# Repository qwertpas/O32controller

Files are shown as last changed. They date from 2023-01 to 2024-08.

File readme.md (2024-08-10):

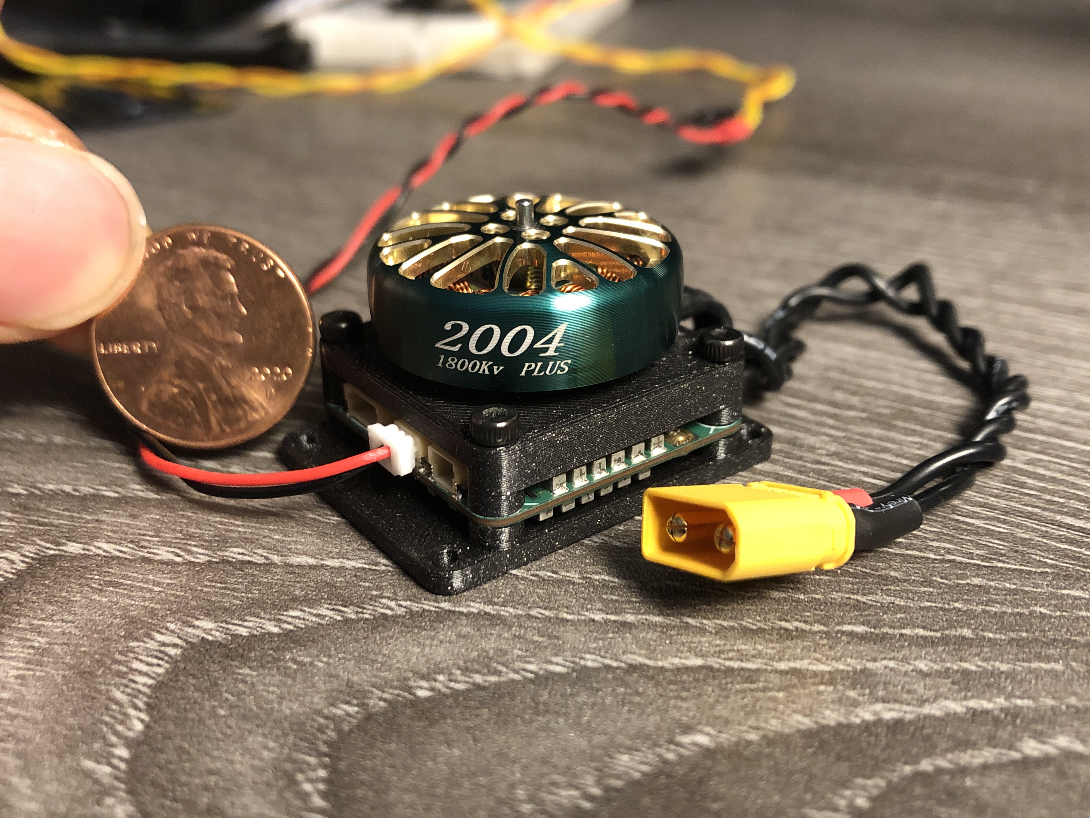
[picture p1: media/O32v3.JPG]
BR2304

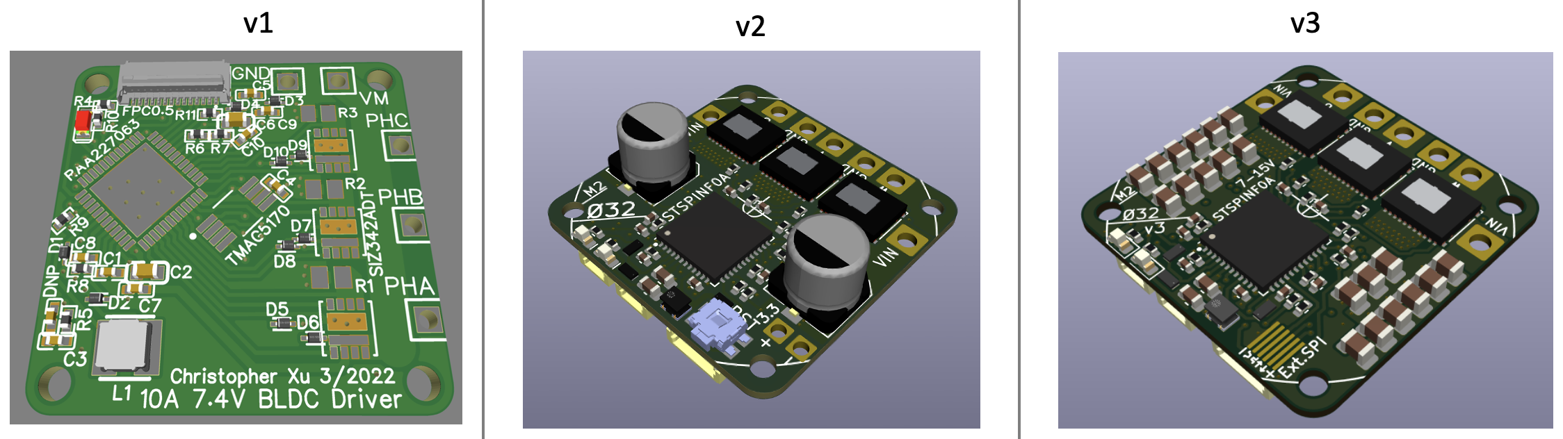
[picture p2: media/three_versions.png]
threeversions


Small robots often use servos or small brushed DC motors, but they are not as power dense as the brushless DC (BLDC) motors commonly found in drones. Called the Ø32 because the M2 mounting holes are on a 32mm diameter circle, this project controls 7-15V motors with accurate position feedback and field-oriented control (FOC), while fitting almost completely behind a 2304 or larger drone motor.

Specs:
- 27mm x 27mm x 0.8mm, 4-layer, 1oz copper PCB
- M2 mounting holes on a 32mm diameter circle
- 7-15V input, bus voltage sensing
- MCU internal temperature sensor and external NTC reading
- built-in high speed 12-bit magnetic angle sensor and external SPI encoder port (3.3V)
- 3 shunt current sensing and overcurrent protection 
- 2x 2-pin JST-SH connectors for RS-485 communication, allowing daisy chaining
- 1x 4-pin JST-SH connector for SWD programming/debug and UART_TX output
- FOC capable

Critical components:
- STSPIN32F0A BLDC gate driver and Cortex-M0 MCU
- MA702 magnetic angle sensor
- CSD88584Q5DC half-bridge (50A continuous)

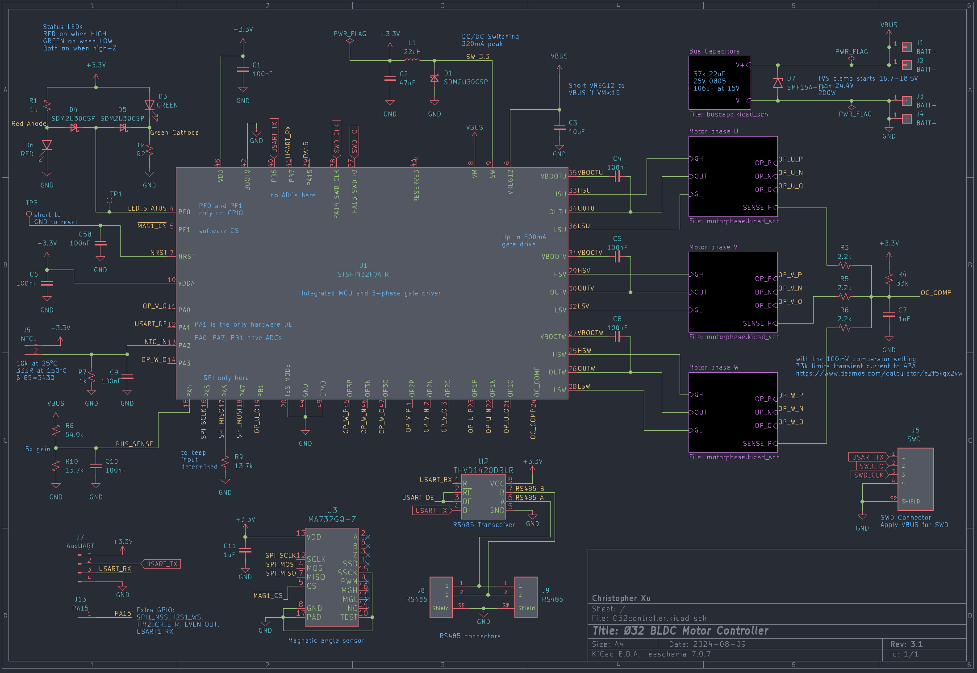
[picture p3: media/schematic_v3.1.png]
schematic

[Full schematic PDF](https://github.com/qwertpas/O32controller/blob/master/v3/output_v3.1/O32controller.pdf)

More info on Hackaday.io: https://hackaday.io/project/189115-32-bldc-controller

Firmware here: https://github.com/qwertpas/O32controller_FW

Changelog from v3 to v3.1:
- Larger 15V TVS diode D2 (SMF15A) because there is space 
- Changed R4 from 121kΩ to 33kΩ for a more reasonable phase current limit of 43A using the 100mV comparator 
- Replaced external SPI pads with UART and GPIO PA15 pads for direct communication with another microcontroller without need for RS485 transceiver 
- Replace MA702 (12-bit magnetic encoder) with MA732 (14-bit, adjustable filter)
- Picked out parts in stock from LCSC as much as possible

Changelog from v2 to v3:
- Fixed TVS diode direction on VBUS (!!)
- Changed to 37x 22uF ceramic capacitors instead of 2x 100uF electrolytic capacitors for a thinner PCBA
- Removed I2C (formerly on PB6 and PB7)
- Moved UART_TX and UART_RX to PB6 and PB7 (formerly on PA2 and PA15)
- Changed PA2 to ADC1 CH2 to read a 10k NTC, soldered to pads
- Changed PA15 to GPIO for external SPI CS (MAG2_CS)
- Added 13.7k pulldown on SPI_MISO to keep it determined when no devices selected
- Changed to 100nF filter capacitor on BUS_SENSE instead of 1nF to charge ADC capacitor better and for smoother data
- Changed BUS_SENSE gain to 5x instead of 5.12x to reuse 13.7k resistor
- Removed test point on BUS_SENSE
- Added test point on LED_STATUS (for debugging using GPIO)
- Removed NRST pushbutton to create space
- Added 6 pads with 0.5mm pitch to solder FFC cable for an external SPI encoder
- Changed vias to 0.25mm hole size and 0.55mm plated diameter instead of 0.2/0.5 for easier manufacturability
- Changed minimum track clearance from 0.2mm to 0.16mm to make space for larger vias
- Changed to equal number of vias (27) on the top side of all three shunt resistors
- Changed most silkscreen text to 0.8mm width/height
- Put all footprints and 3D models in project library O32controller

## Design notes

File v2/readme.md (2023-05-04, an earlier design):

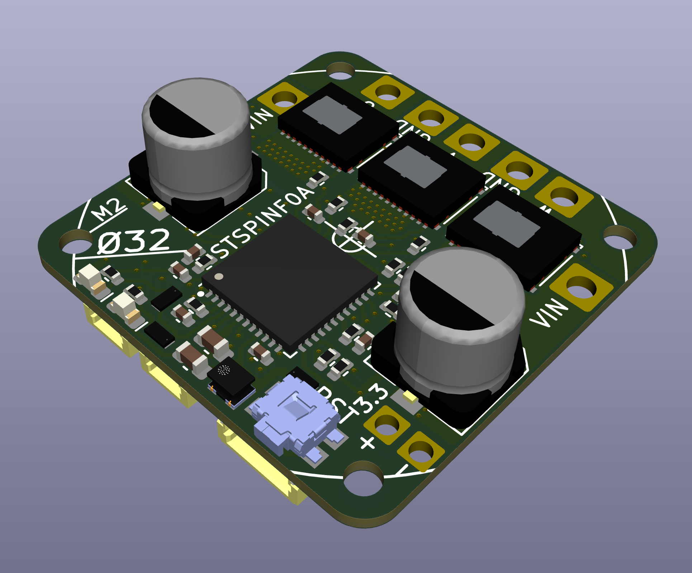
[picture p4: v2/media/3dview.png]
3dview


a brushless DC motor controller that fits behind a small drone motor (mounting holes are 32mm in diameter)

Board components are rated for 15V, 50A continuous and 110A for 10 seconds.  

Firmware here: https://github.com/qwertpas/O32controller_FW

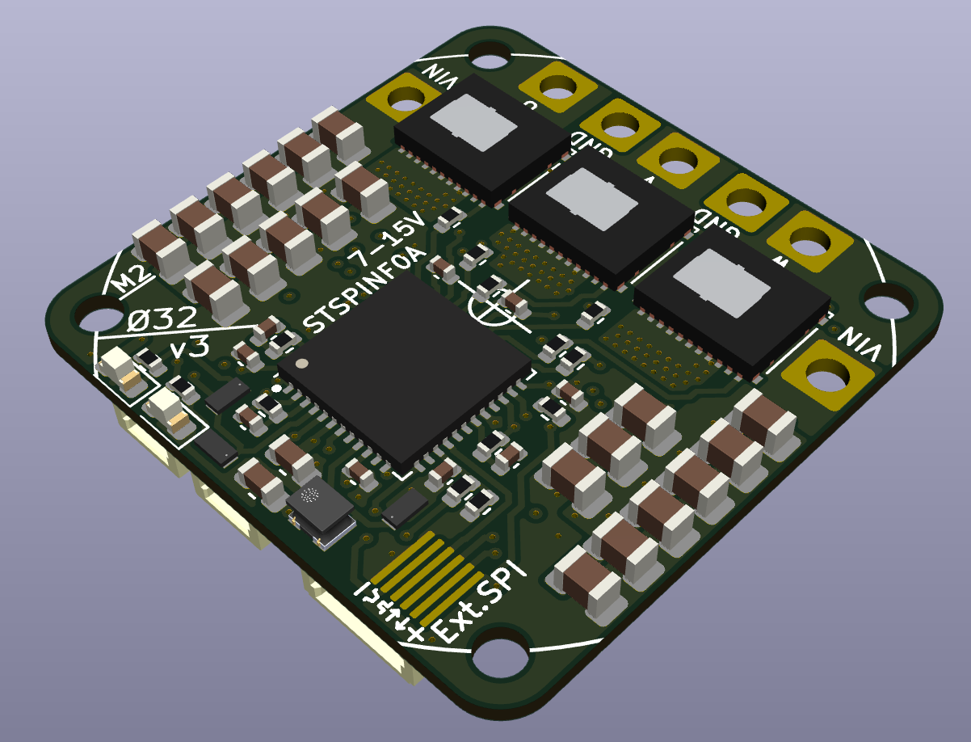
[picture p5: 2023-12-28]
media/v3_3d_front.png

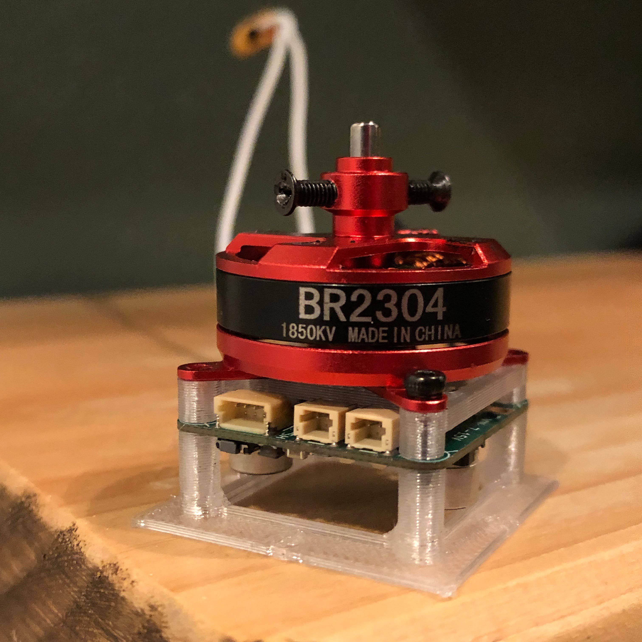
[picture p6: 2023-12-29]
media/O32_BR2304.jpeg

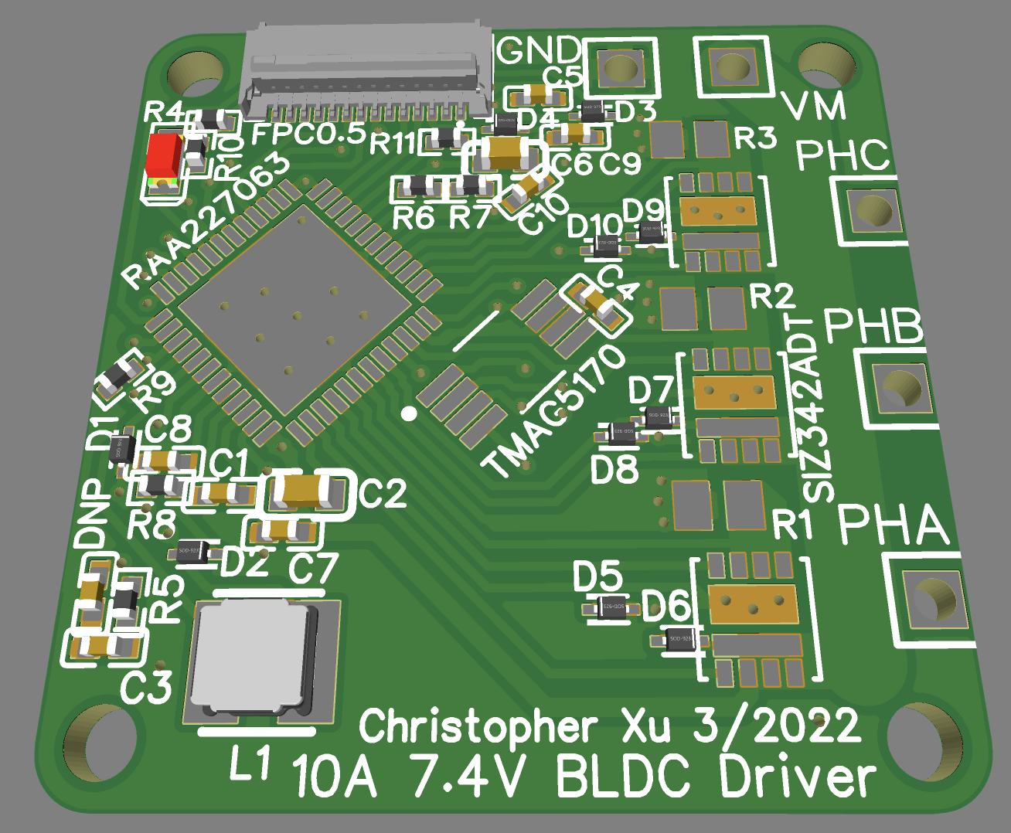
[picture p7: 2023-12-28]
media/v1_3d_front.png

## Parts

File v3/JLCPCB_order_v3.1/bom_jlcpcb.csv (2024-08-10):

Comment | Designator | Footprint | LCSC
100nF | C1,C4,C5,C6,C8,C9,C10,C58 | Capacitor_SMD:C_0402_1005Metric | C307331
1uF | C11 | Capacitor_SMD:C_0402_1005Metric | C52923
10nF | C12,C15,C18 | Capacitor_SMD:C_0402_1005Metric | C15195
4.7nF | C13,C16,C19 | Capacitor_SMD:C_0402_1005Metric | C1538
47uF | C2 | Capacitor_SMD:C_0603_1608Metric | C140782
22uF | C21,C22,C23,C24,C25,C26,C27,C28,C29,C30,C31,C32,C33,C34,C35,C36,C37,C38,C39,C40,C41,C42,C43,C44,C45,C46,C47,C48,C49,C50,C51,C52,C53,C54,C55,C56,C57 | O32controller:C_0805_nosilk | C45783
10uF | C3 | Capacitor_SMD:C_0603_1608Metric | C194427
1nF | C7,C14,C17,C20 | Capacitor_SMD:C_0402_1005Metric | C1523
SDM2U30CSP | D1,D4,D5 | O32controller:SDM2U30CSP-7
GREEN | D3 | LED_SMD:LED_0603_1608Metric | C125098
RED | D6 | LED_SMD:LED_0603_1608Metric | C2286
SMF15A-TP | D7 | Diode_SMD:D_SMF | C914420
SWD | J6 | O32controller:JST_SM04B-SRSS-TB(LF)(SN)
RS485 | J8,J9 | O32controller:JST_SM02B-SRSS-TB(LF)(SN) | C160402
22uH | L1 | O32controller:IND_VLS201612CX-220M-1 | C2044426
CSD88584Q5DC | Q1,Q2,Q3 | O32controller:CSD88584Q5DCT
1k | R1,R2,R7 | Resistor_SMD:R_0402_1005Metric | C11702
10R | R11,R13,R20,R22,R29,R31 | Resistor_SMD:R_0402_1005Metric | C854481
2.2R | R12,R21,R30 | Resistor_SMD:R_0402_1005Metric | C131536
27.4k | R14,R16,R23,R25,R32,R34 | Resistor_SMD:R_0402_1005Metric | C273730
1.78k | R15,R17,R24,R26,R33,R35 | Resistor_SMD:R_0402_1005Metric | C284379
PU2512FKMP50R002L | R18,R27,R36 | O32controller:R_Shunt_2512_6332Metric | C2090861
2.2k | R3,R5,R6 | Resistor_SMD:R_0402_1005Metric | C25879
33k | R4 | Resistor_SMD:R_0402_1005Metric | C25779
54.9k | R8 | Resistor_SMD:R_0402_1005Metric | C137959
13.7k | R9,R10,R19,R28,R37 | Resistor_SMD:R_0402_1005Metric | C274888
STSPIN32F0ATR | U1 | O32controller:VFQFPN-48-1EP_7x7mm_P0.5mm_EP2.8x2.8mm | C2651733
THVD1420DRLR | U2 | O32controller:THVD1420DRLR_SOT-585
MA732GQ-Z | U3 | O32controller:QFN-16_MA732

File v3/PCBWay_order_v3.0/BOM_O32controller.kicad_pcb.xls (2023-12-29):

designator | quantity | value | pack | mpn | mount_type
C1, C10, C4, C5, C58, C6, C8, C9 | 8 | 100nF | C_0402_1005Metric | CL05A104KA5NNNC | smt
C11 | 1 | 1uF | C_0402_1005Metric | GCM155C71A105KE38D | smt
C12, C15, C18 | 3 | 10nF | C_0402_1005Metric | CL05B103KB5NNNC | smt
C13, C16, C19 | 3 | 4.7nF | C_0402_1005Metric | GRM155R72A472KA01D | smt
C14, C17, C20, C7 | 4 | 1nF | C_0402_1005Metric | CC0402MRX7R9BB102 | smt
C2 | 1 | 47uF | C_0603_1608Metric | GRM188R60J476ME15D | smt
C21, C22, C23, C24, C25, C26, C27, C28, C29, C30, C31, C32, C33, C34, C35, C36, C37, C38, C39, C40, C41, C42, C43, C44, C45, C46, C47, C48, C49, C50, C51, C52, C53, C54, C55, C56, C57 | 37 | 22uF | C_0805_nosilk | CL21A226MAQNNNE | smt
C3 | 1 | 10uF | C_0603_1608Metric | GRM188R6YA106MA73D | smt
D1, D4, D5 | 3 | SDM2U30CSP | SDM2U30CSP-7 | SDM2U30CSP-7 | smt
D2 | 1 | ESDA17P20-1F2 | SMT2_0P91X0P63_STM-L | ESDA17P20-1F2 | smt
D3 | 1 | GREEN | LED_0603_1608Metric | LTST-C191KGKT | smt
D6 | 1 | RED | LED_0603_1608Metric | LTST-C191KRKT | smt
J1, J2 | 2 | BATT+ | SolderWire-Actual_1x01_D1.7mm_OD_2.75mm |  | tht
J10, J11, J12 | 3 | Motor Connection | SolderWire-Actual_1x01_D1.7mm_OD_2.75mm |  | tht
J3, J4 | 2 | BATT- | SolderWire-Actual_1x01_D1.7mm_OD_2.75mm |  | tht
J5 | 1 | NTC | SolderNTC-1.27mm |  | tht
J6 | 1 | SWD | JST_SM04B-SRSS-TB(LF)(SN) | SM04B-SRSS-TB(LF)(SN) | smt
J7 | 1 | ExternalSPI | FFC_0.5mm_6p |  | tht
J8, J9 | 2 | RS485 | JST_SM02B-SRSS-TB(LF)(SN) | SM02B-SRSS-TB_LF__SN_ | smt
L1 | 1 | 22uH | IND_VLS201612CX-220M-1 | VLS201612CX-220M-1 | smt
NT1, NT2, NT3 | 3 | Sense_N | NetTie-2_SMD_Pad0.25mm |  | tht
Q1, Q2, Q3 | 3 | CSD88584Q5DC | CSD88584Q5DCT | CSD88584Q5DC | smt
R1, R2, R7 | 3 | 1k | R_0402_1005Metric | RC0402FR-071KL | smt
R10, R19, R28, R37, R9 | 5 | 13.7k | R_0402_1005Metric | RC0402FR-0713K7L | smt
R11, R13, R20, R22, R29, R31 | 6 | 10R | R_0402_1005Metric | SR0402FR-7T10RL | smt
R12, R21, R30 | 3 | 2.2R | R_0402_1005Metric | CRCW04022R20JNEDHP | smt
R14, R16, R23, R25, R32, R34 | 6 | 27.4k | R_0402_1005Metric | RC0402FR-0727K4L | smt
R15, R17, R24, R26, R33, R35 | 6 | 1.78k | R_0402_1005Metric | RC0402FR-071K78L | smt
R18, R27, R36 | 3 | PU2512FKMP50R002L | R_Shunt_2512_6332Metric | PU2512FKMP50R002L | smt
R3, R5, R6 | 3 | 2.2k | R_0402_1005Metric | RC0402FR-072K2L | smt
R4 | 1 | 121k | R_0402_1005Metric | AF0402FR-07121KL | smt
R8 | 1 | 54.9k | R_0402_1005Metric | RC0402FR-0754K9L | smt
TP1, TP3 | 2 | TestPoint | TestPoint_Pad_Rect |  | tht
U1 | 1 | STSPIN32F0ATR | VFQFPN-48-1EP_7x7mm_P0.5mm_EP2.8x2.8mm | STSPIN32F0ATR | smt
U2 | 1 | THVD1420DRLR | THVD1420DRLR_SOT-585 | THVD1420DRLR | smt
U3 | 1 | MA702GQ-P | MA702GQ-P | MA702GQ-P | smt

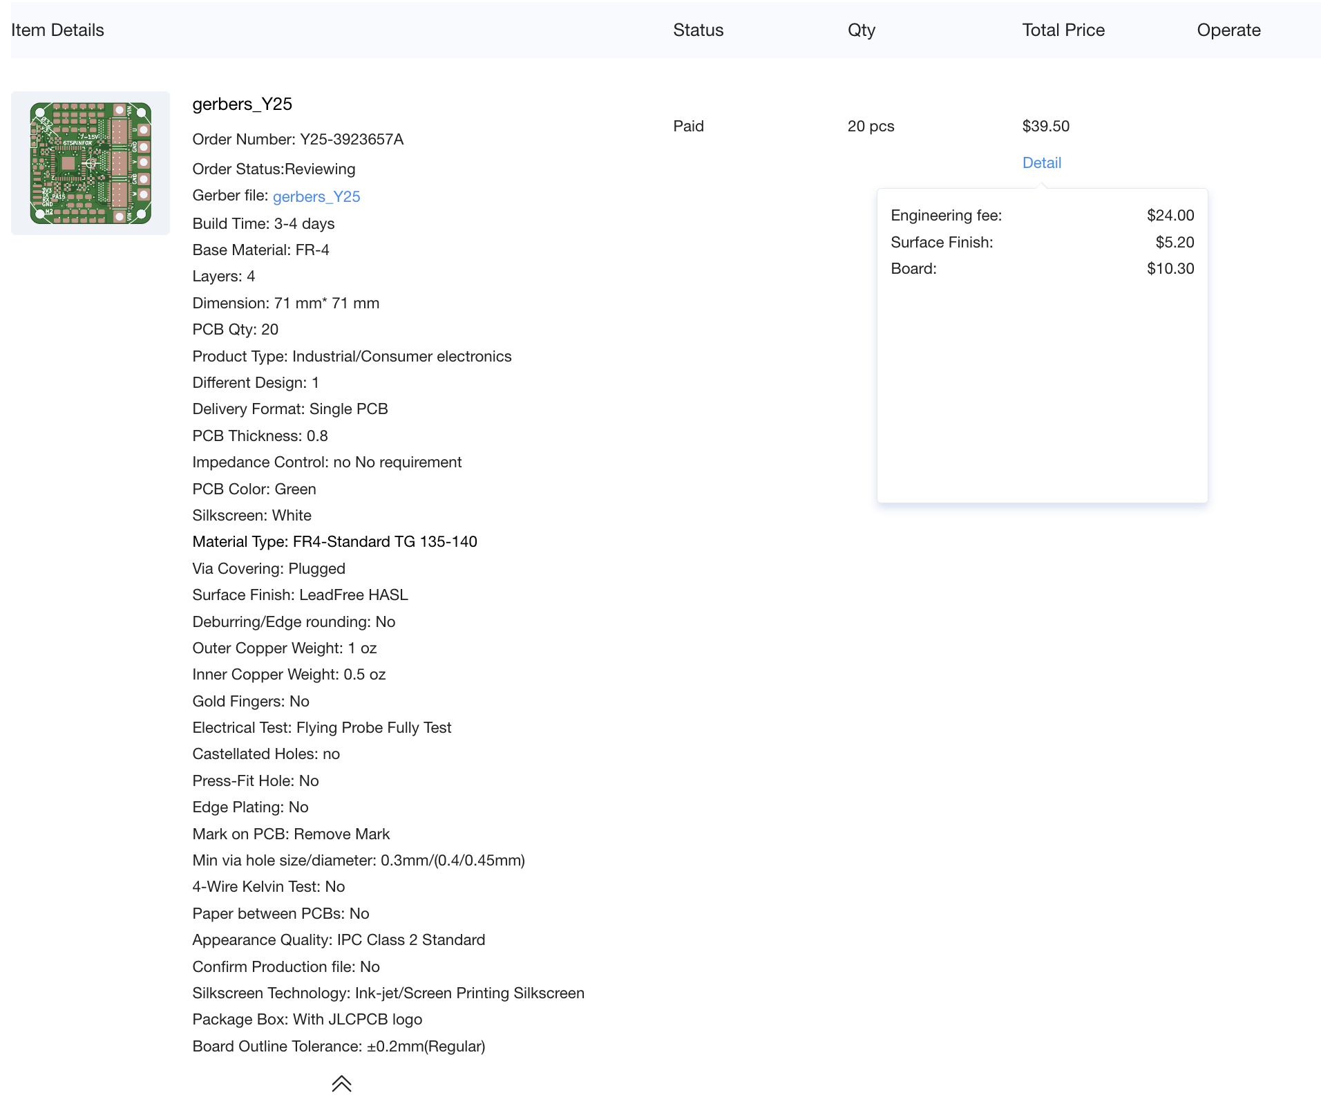
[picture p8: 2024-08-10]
v3/JLCPCB_order_v3.1/pcb_order.png

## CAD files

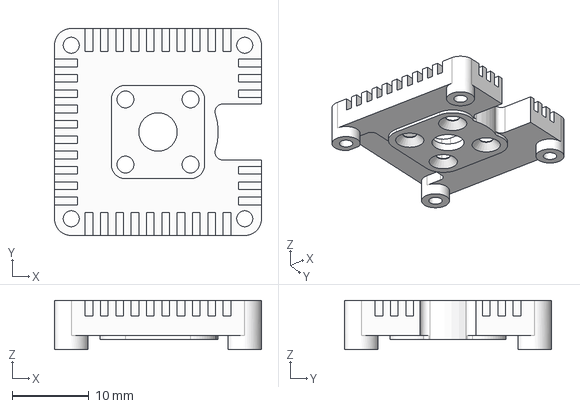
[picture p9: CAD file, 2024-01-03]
heatsinks/greenmount.step
27.0 x 27.0 x 6.40 mm

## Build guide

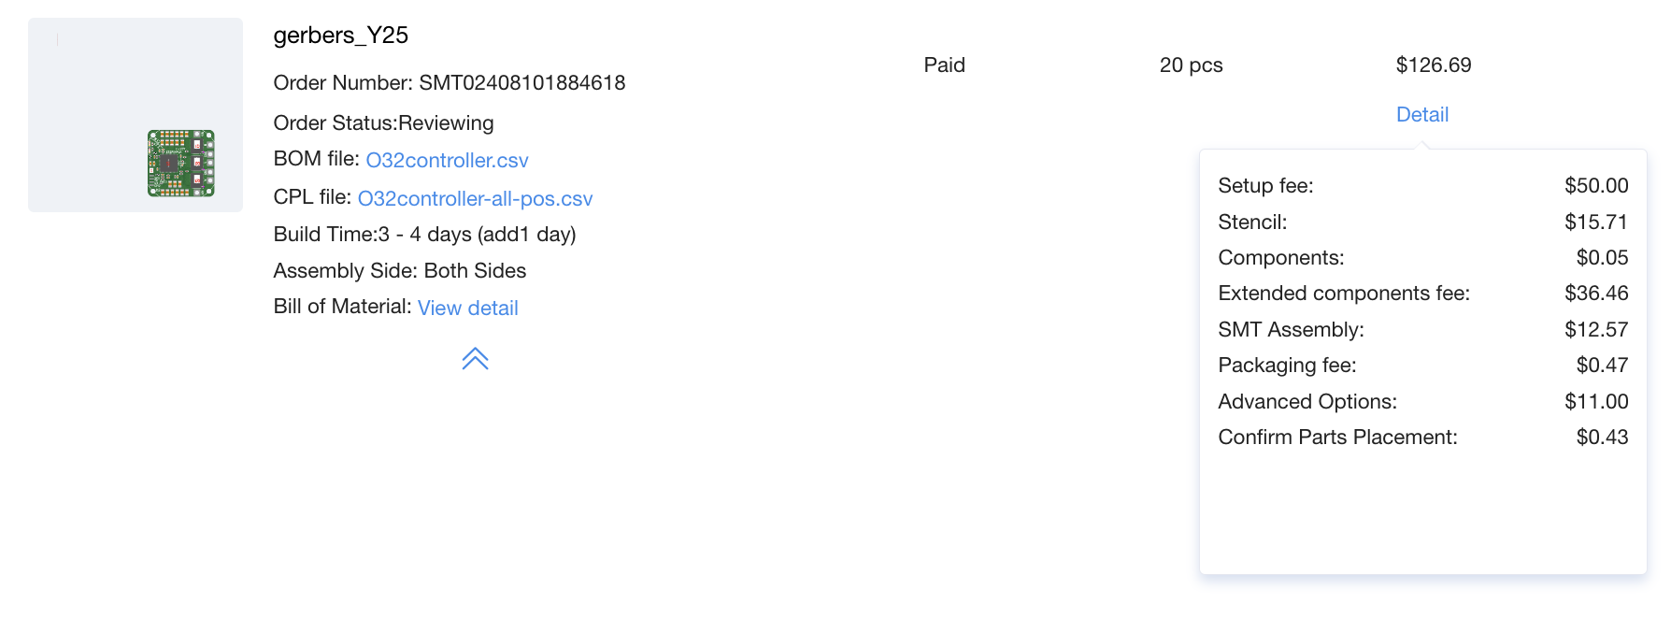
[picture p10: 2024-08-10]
v3/JLCPCB_order_v3.1/assembly_order.png

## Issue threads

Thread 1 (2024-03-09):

increasing the current rating

kavin-x, 2024-03-09:
hi i'm from india can you tell me how to increase the current rating of the board like to handle more than 60A

qwertpas, 2024-03-10:
Hi, the [mosfets I use](https://www.ti.com/product/CSD88584Q5DC) are should handle a maximum of 50A continuous or 400A for very short pulses. It's limited by heat dissipation, so to reach this point you'll need to attach a heatsink to the top of the mosfet package, it conveniently has a large metal pad on top.

kavin-x, 2024-03-11:
Hi thank a lot for replying i know i cant ask you this but im from india and the cost the getting a board assembled here would be a huge amount and i cant afford it as a student i really love your if you dont mind can you assemble the board in your country and ship to be via dhl i'll pay for it so the price will be reduced for me if you can do that it would be really helpful and i could learn a lot with it

kavin-x, 2024-03-11:
I have sent you a mail can you check it?

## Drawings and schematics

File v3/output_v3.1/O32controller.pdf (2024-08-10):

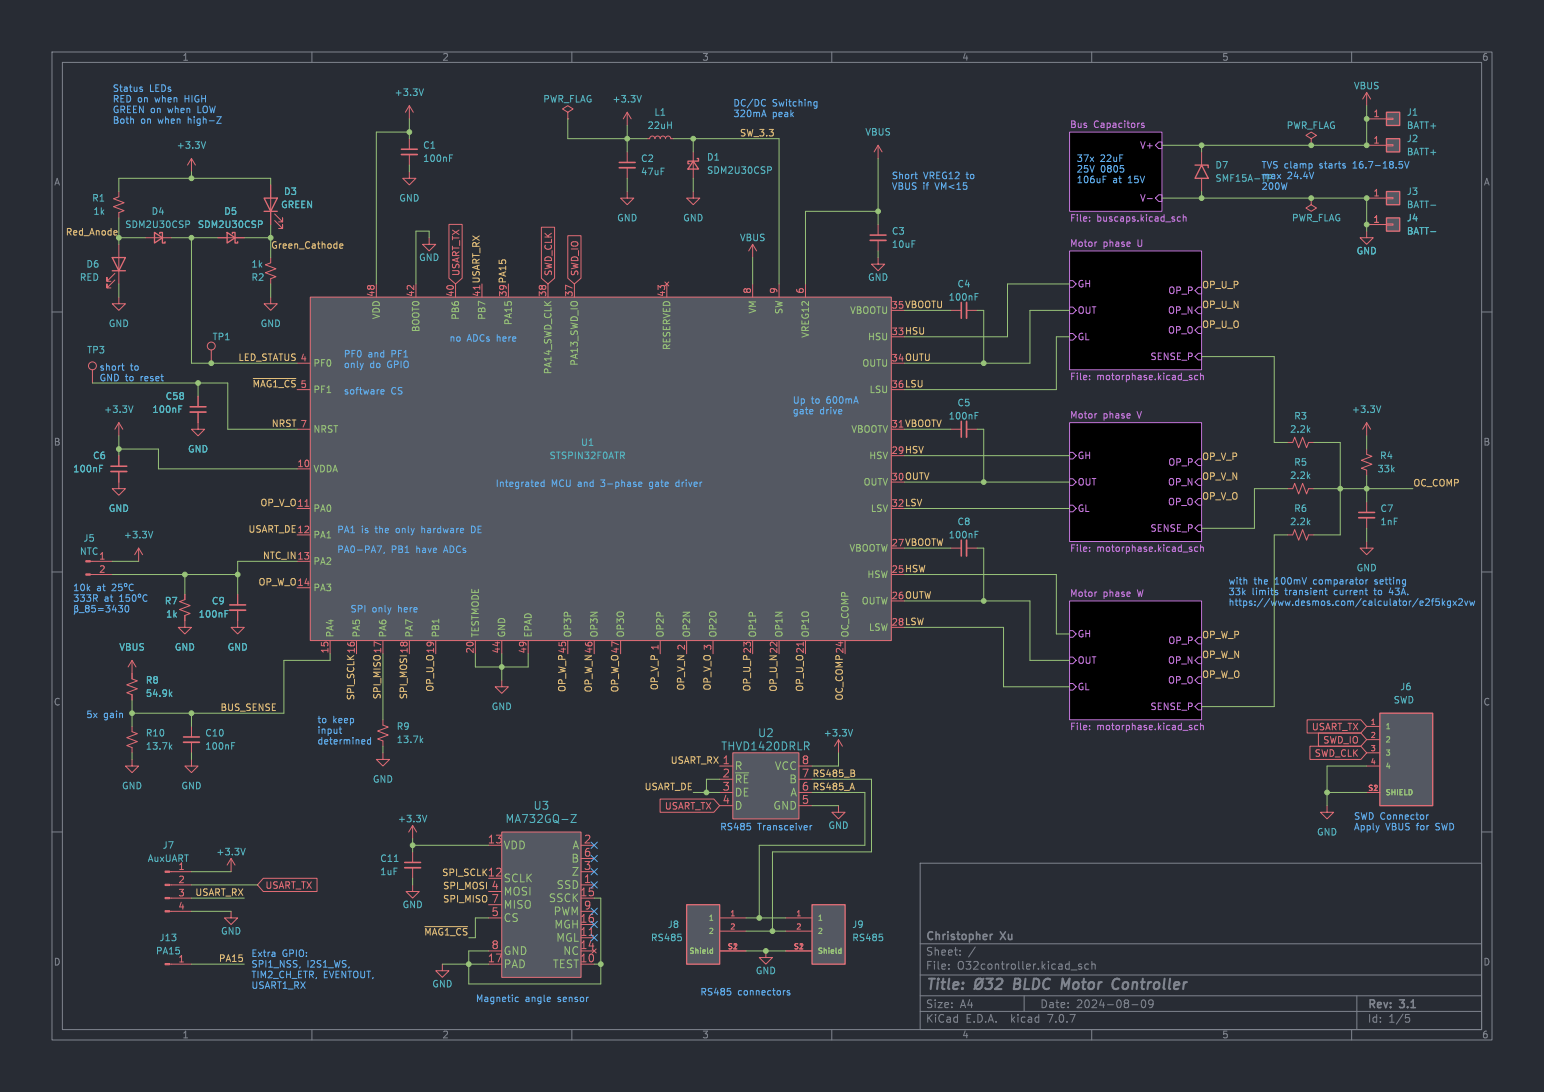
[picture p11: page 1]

Both on when high-Z

V+V- Bus Capacitors File: buscaps.kicad_sch

TVS clamp starts 16.7-18.5V max 24.4V

LSV 32 HSU 33 OUTU 34 VBOOTU 35
VBOOTV HSU

Id: 1/5 Title: þÿØ32BLDC Motor Controller File: O32controller.kicad_sch Sheet: / Christopher Xu

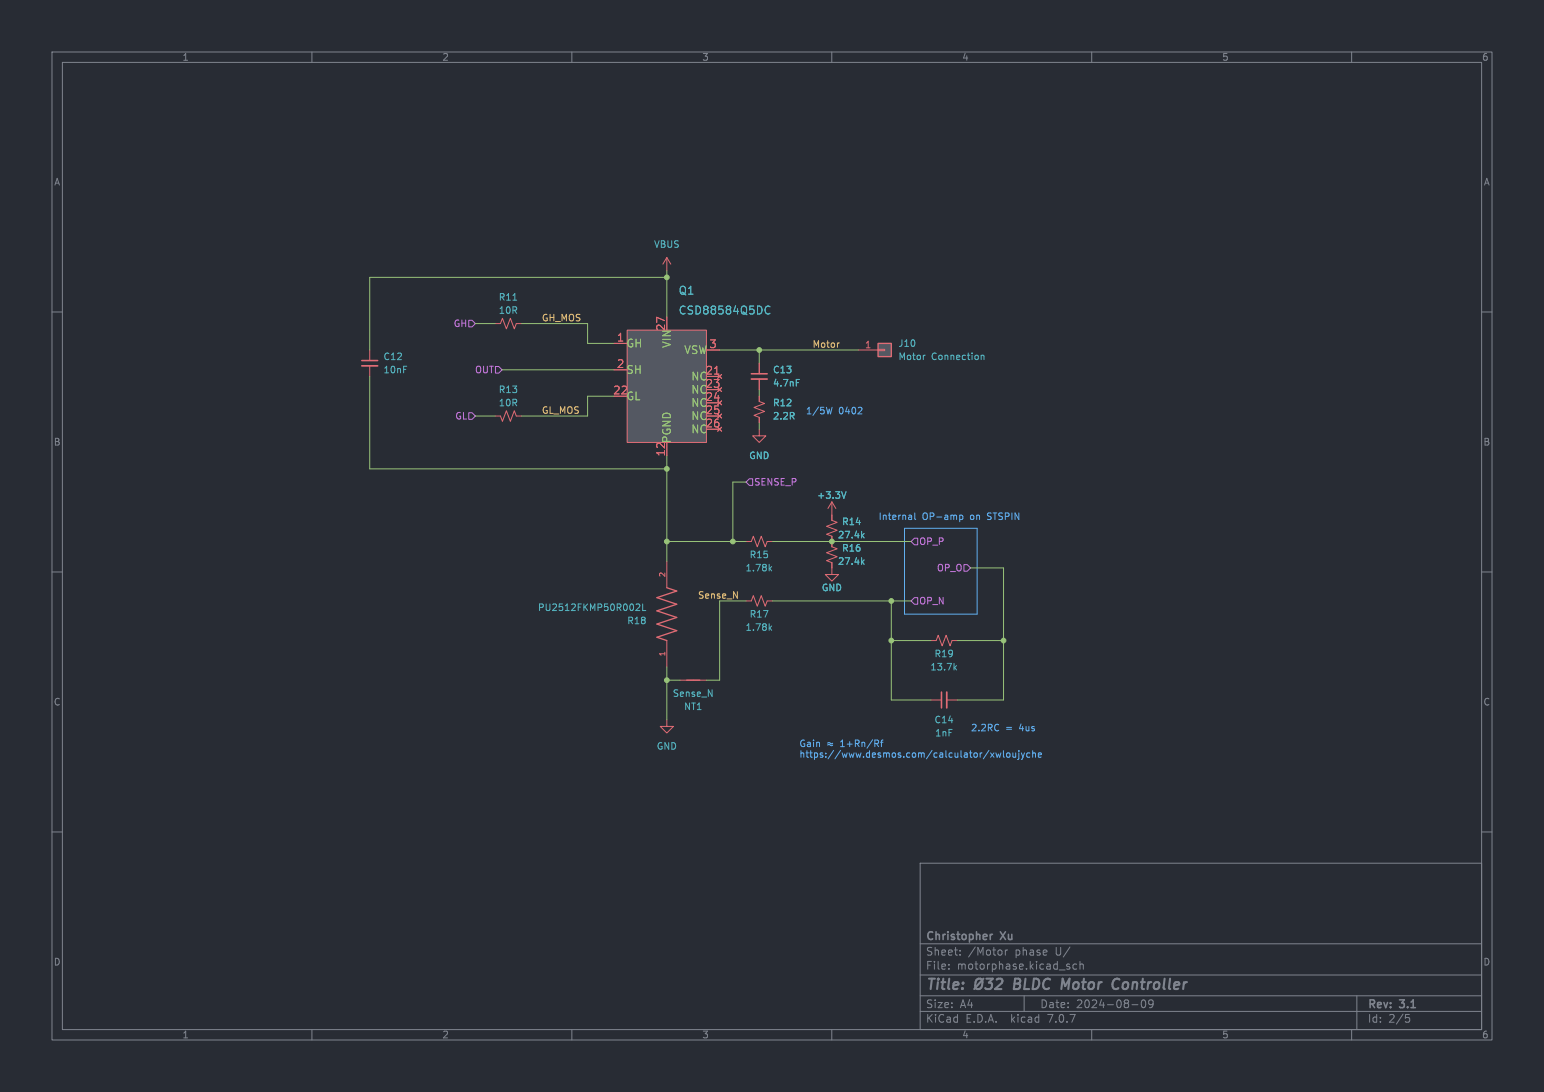
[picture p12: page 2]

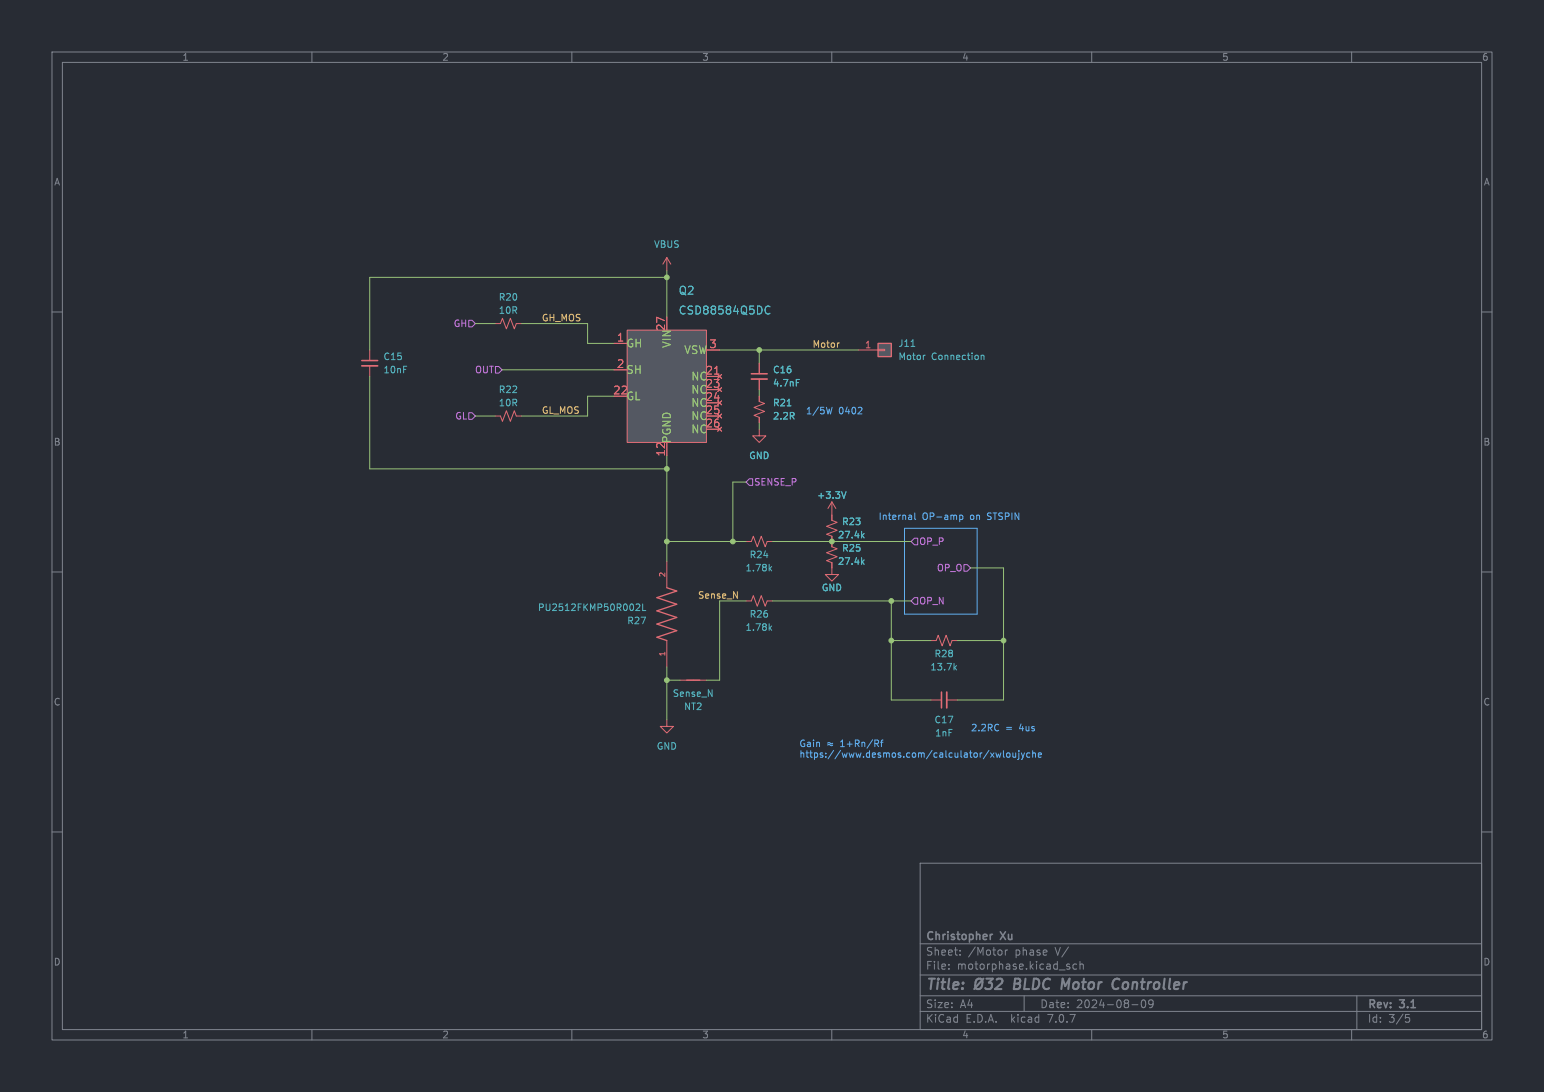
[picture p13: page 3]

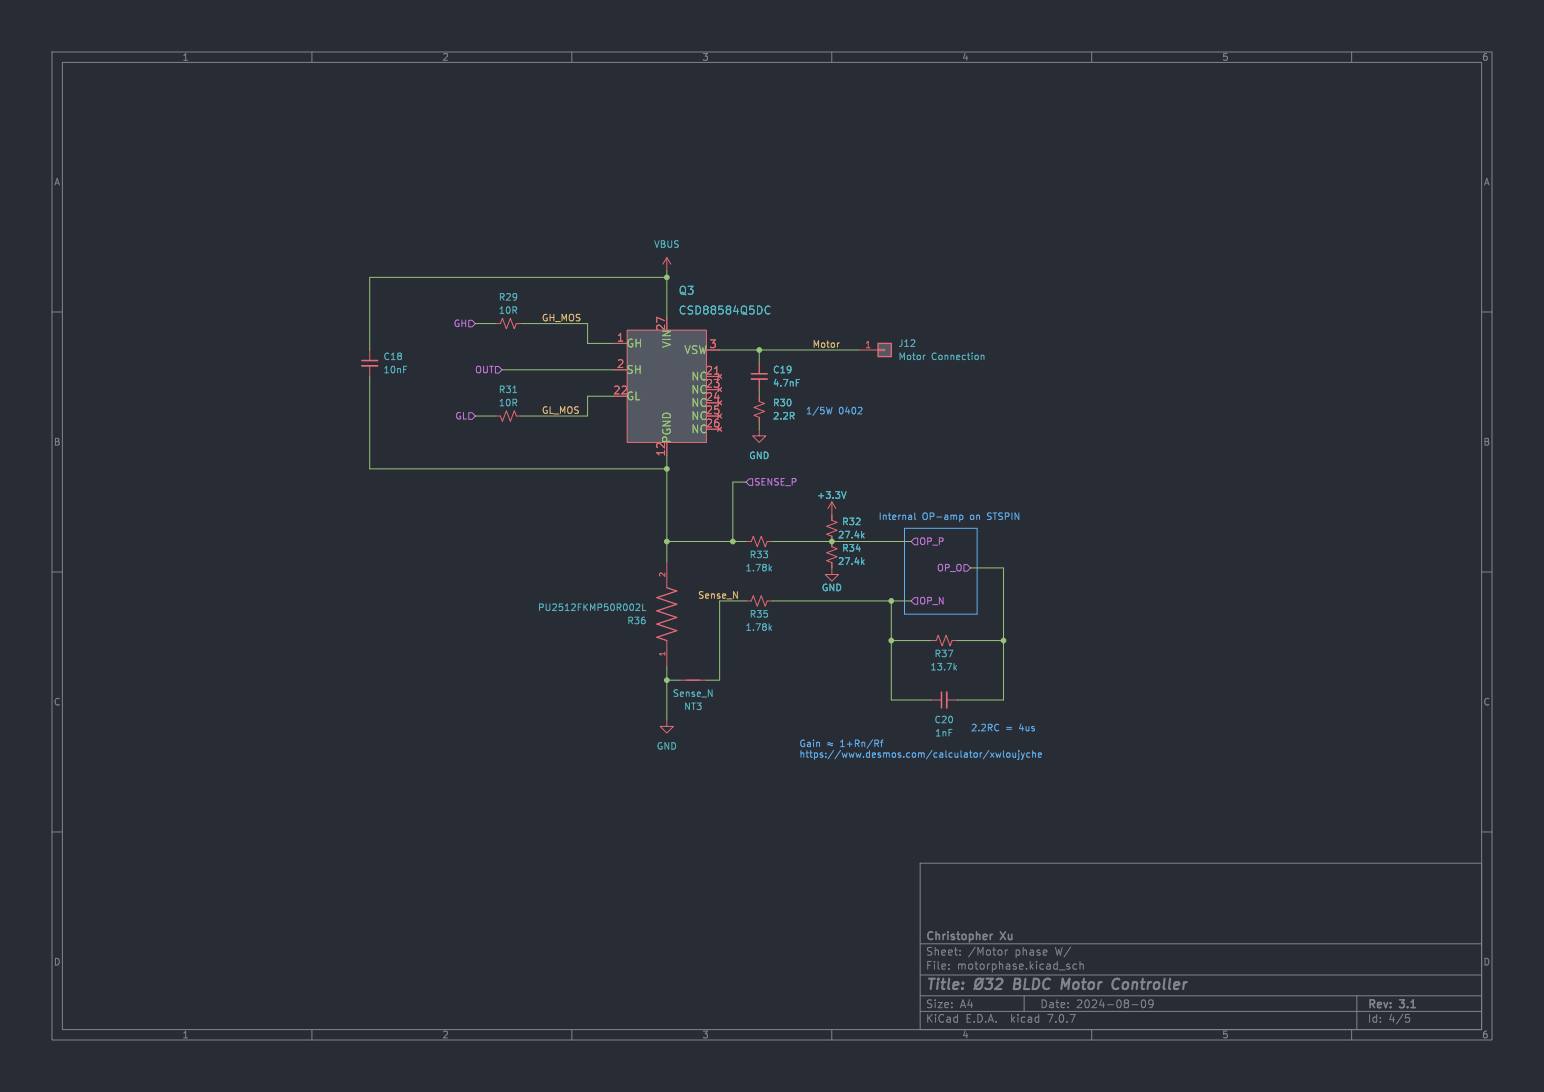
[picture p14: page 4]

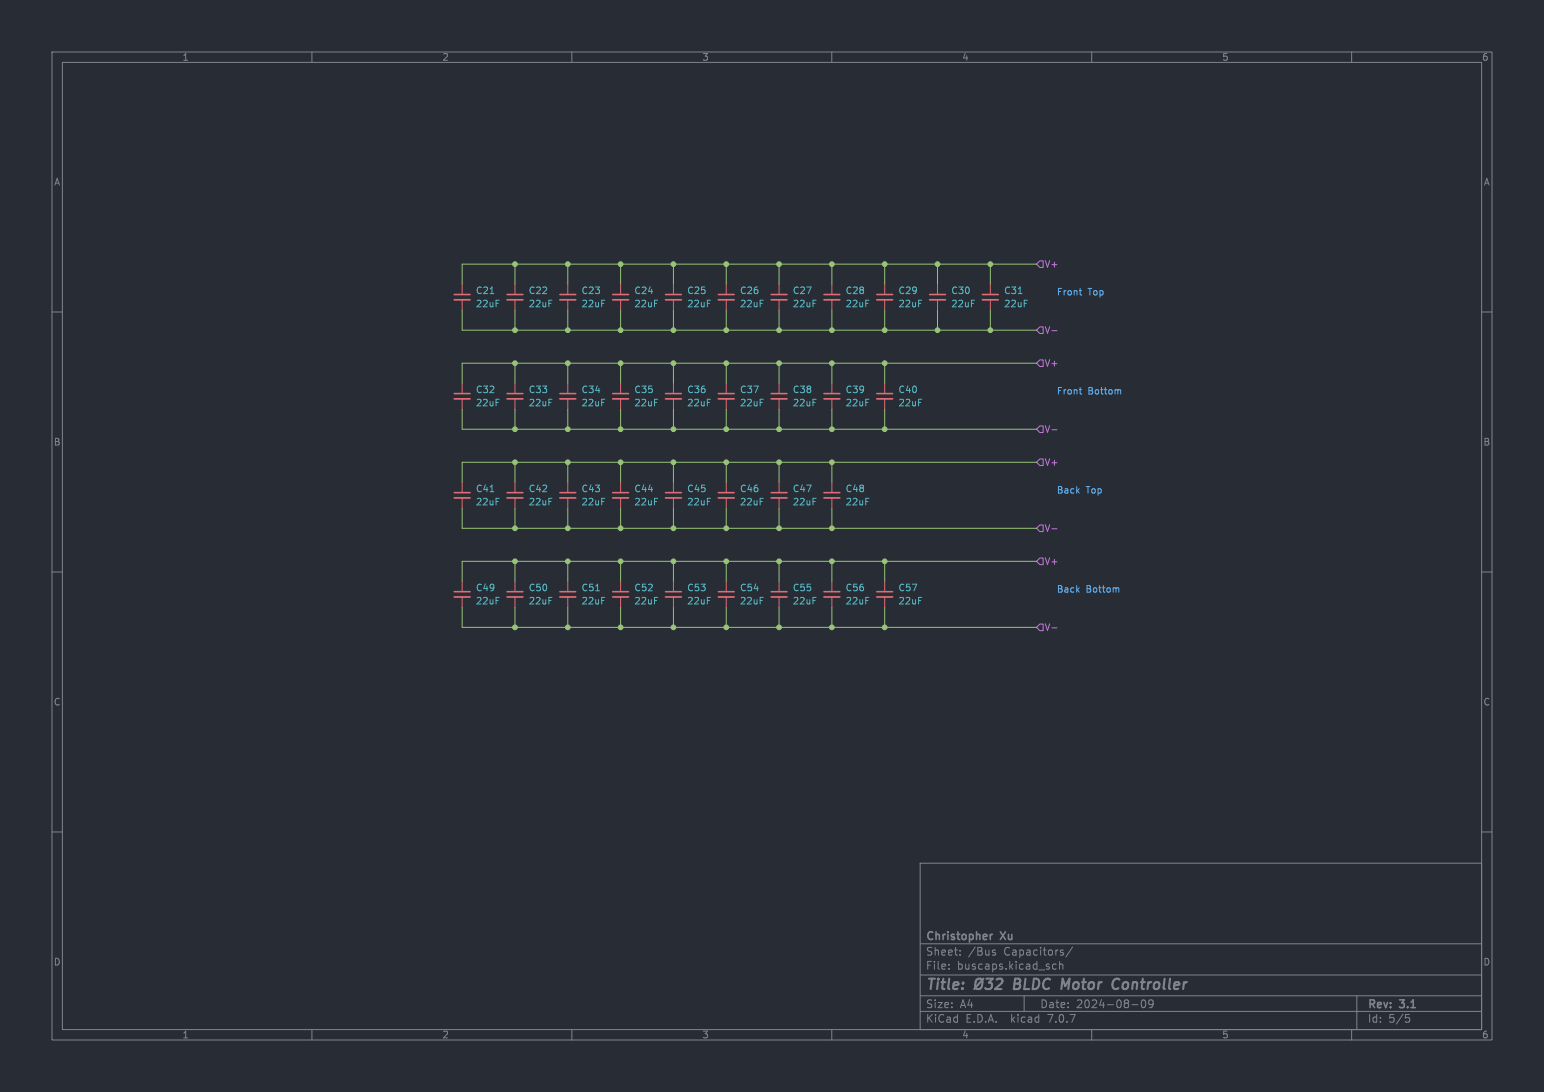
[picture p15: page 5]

Back Top Front Bottom

Id: 5/5 Title: þÿØ32BLDC Motor Controller File: buscaps.kicad_sch Sheet: /Bus Capacitors/

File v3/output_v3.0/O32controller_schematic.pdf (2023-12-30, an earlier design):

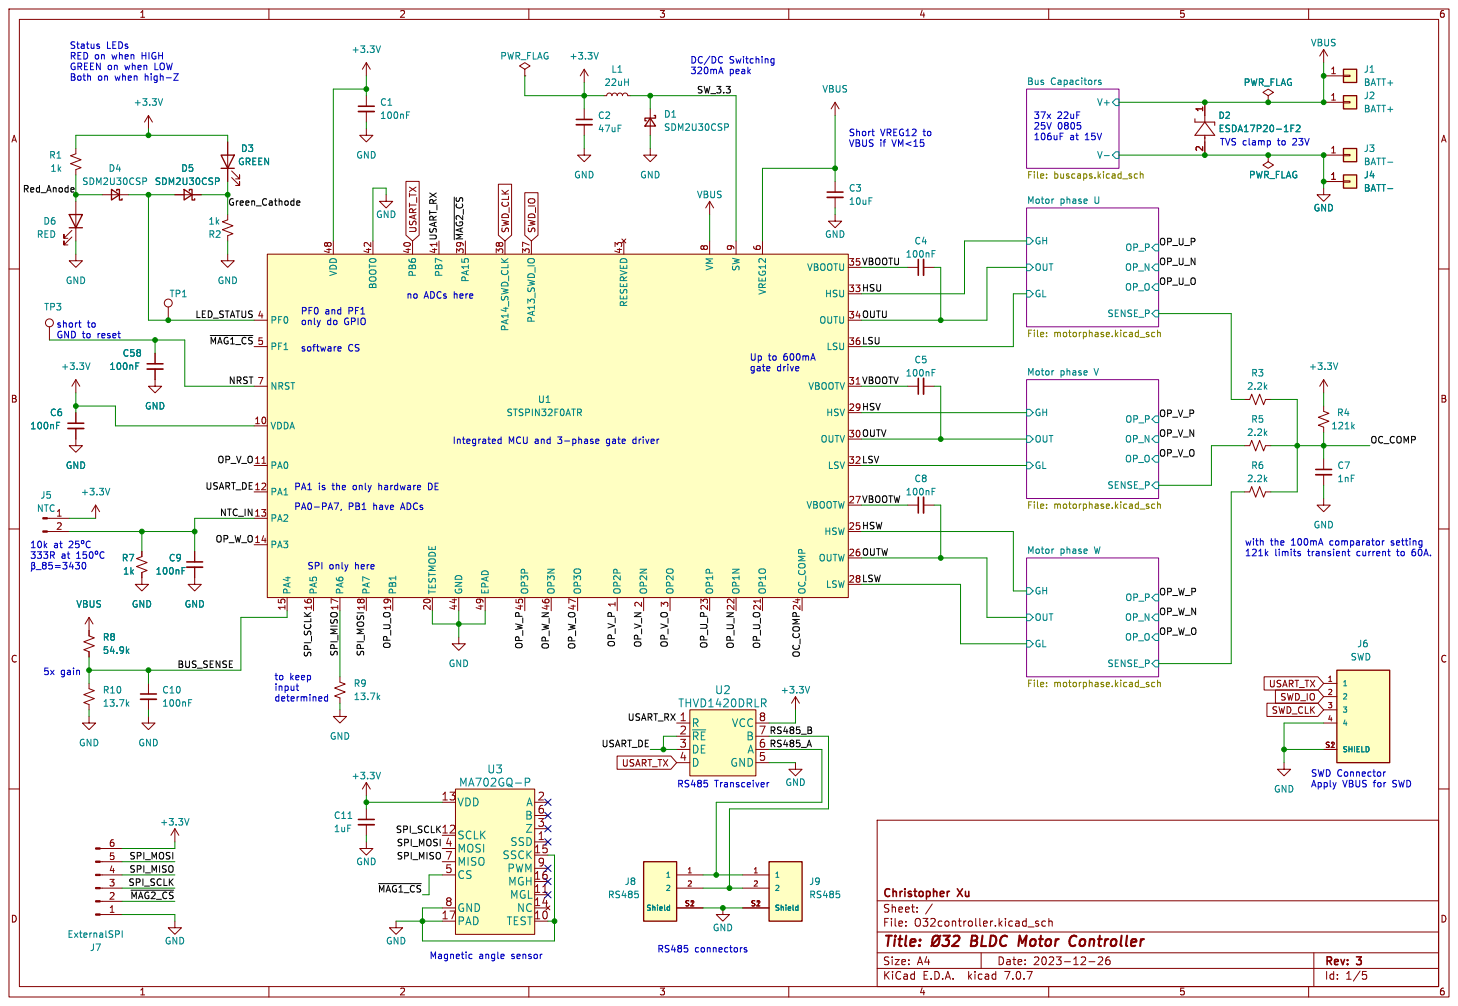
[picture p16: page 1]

Status LEDs RED on when HIGH GREEN on when LOW
+3.3V GND
Both on when high-Z
VBUS C6
D3 GREEN GND

320mA peak no ADCs here

LSV 32 HSU 33 OUTU 34 VBOOTU 35

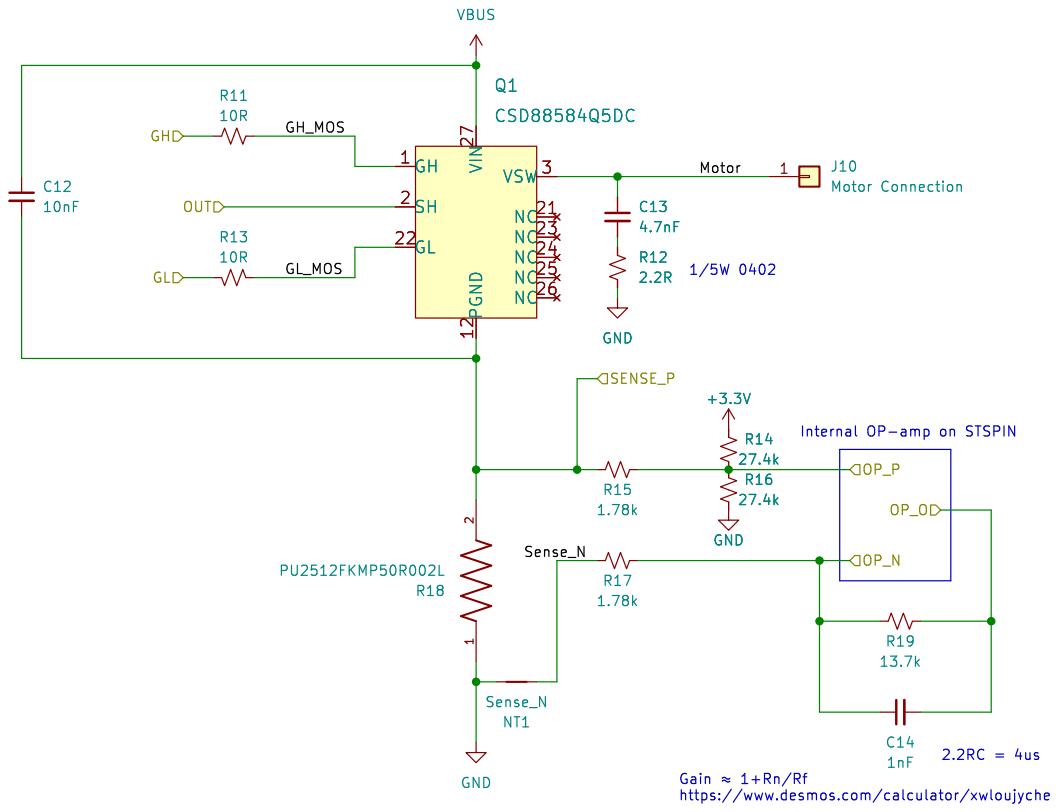
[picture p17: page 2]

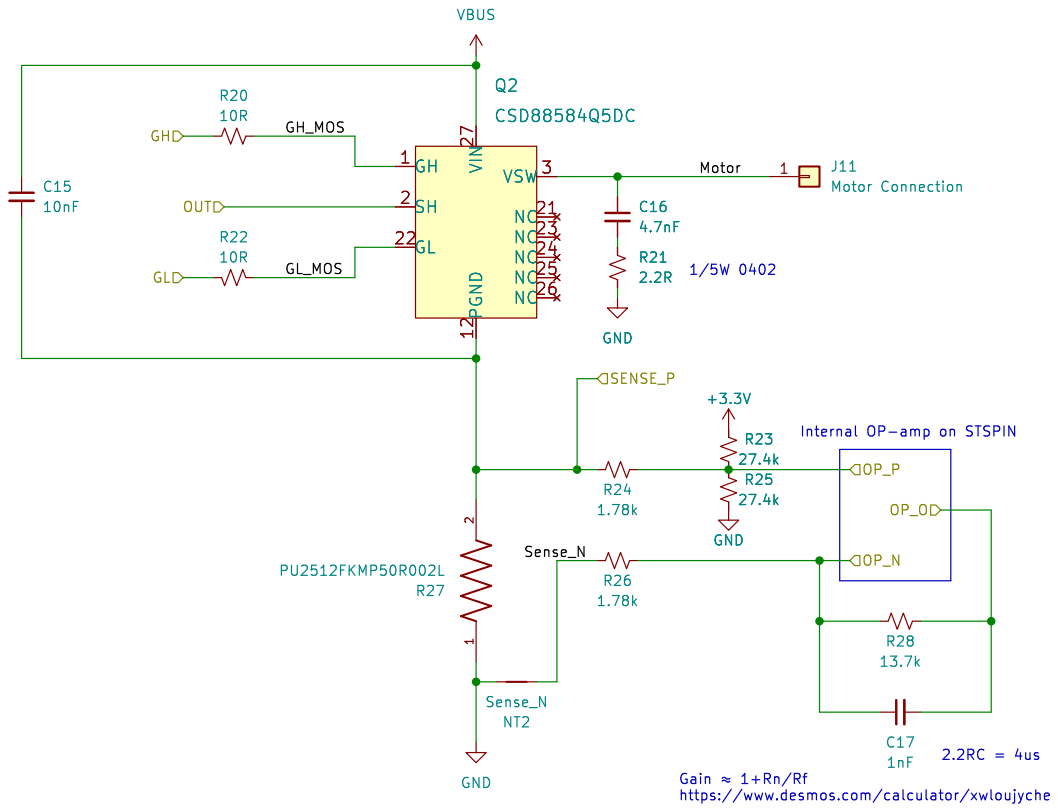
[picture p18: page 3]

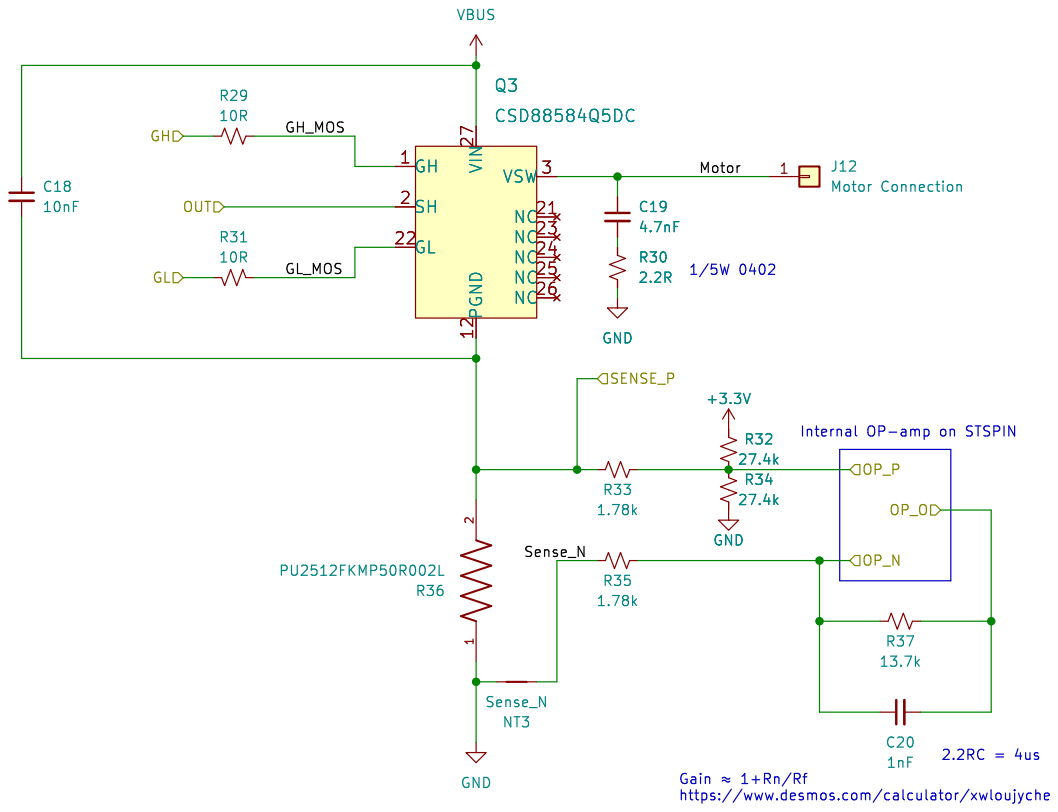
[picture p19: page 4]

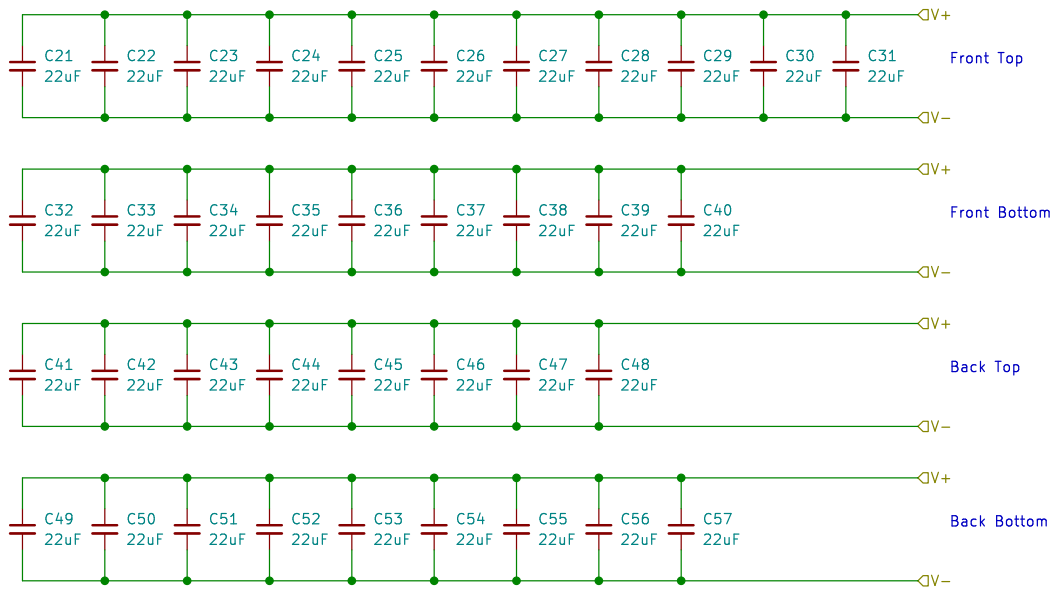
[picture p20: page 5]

Back Top Front Bottom

Id: 5/5 Title: þÿØ32BLDC Motor Controller File: buscaps.kicad_sch Sheet: /Bus Capacitors/

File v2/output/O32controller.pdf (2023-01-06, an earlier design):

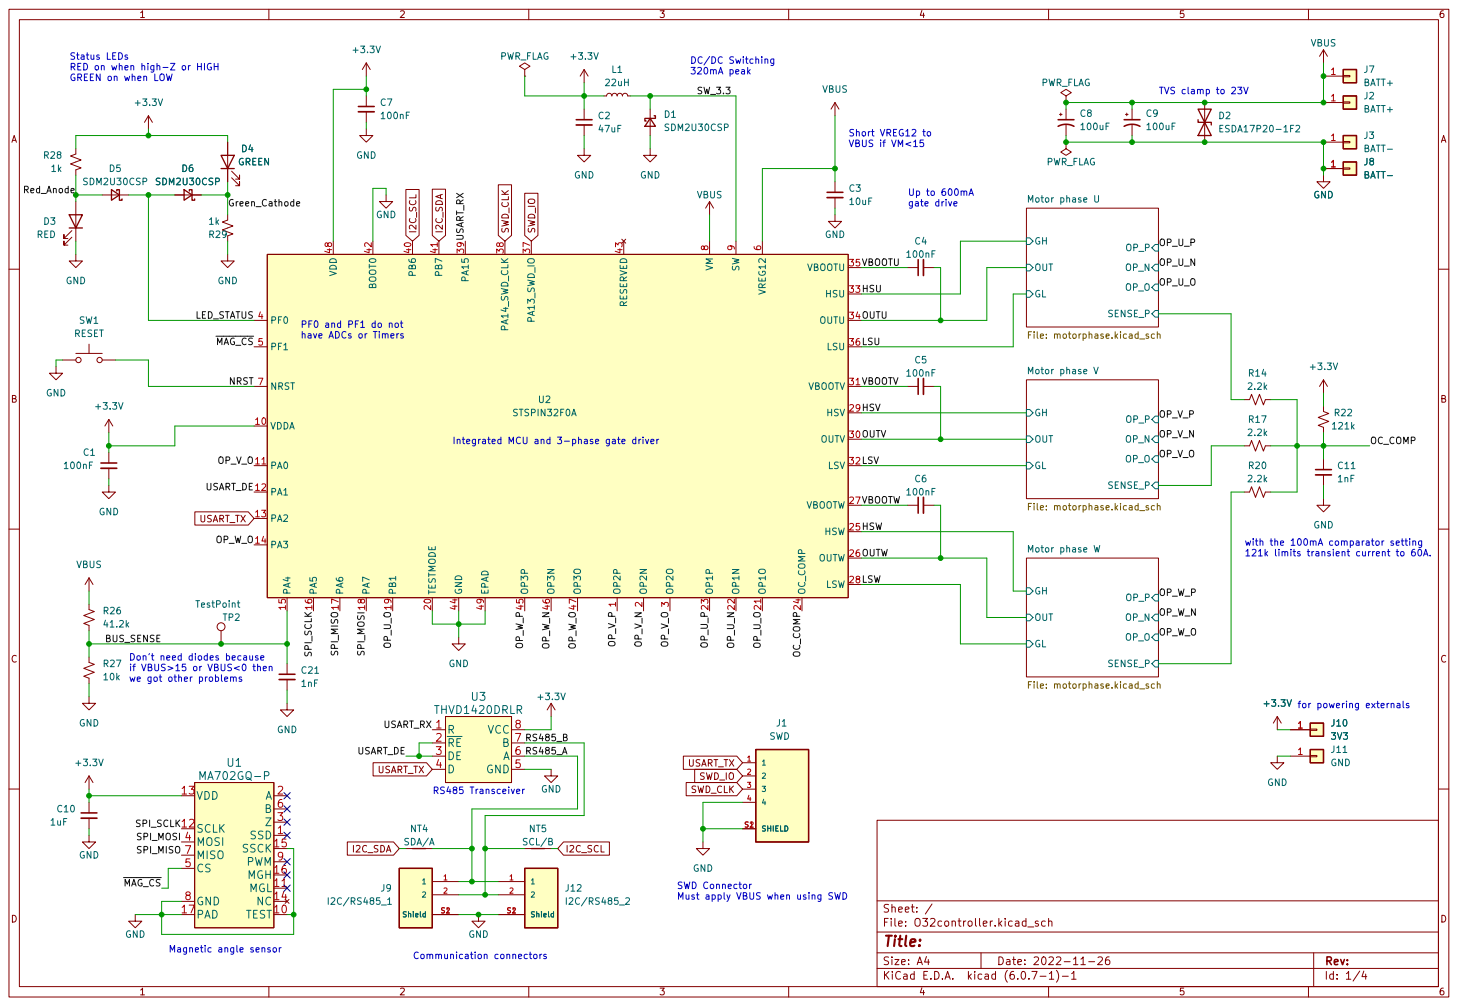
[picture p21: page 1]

gate drive Status LEDs RED on when high-Z or HIGH GREEN on when LOW

TVS clamp to 23V Don't need diodes because

Integrated MCU and 3-phase gate driver

2 TESTMODE 20 OP1O 21 OP1N 22 OP1P 23 OC_COMP 24 HSW 25 OUTW 26 VBOOTW 27

121k limits transient current to 60A. Communication connectors RS485 Transceiver

with the 100mA comparator setting

if VBUS>15 or VBUS<0 then we got other problems

for powering externals SWD Connector Must apply VBUS when using SWD

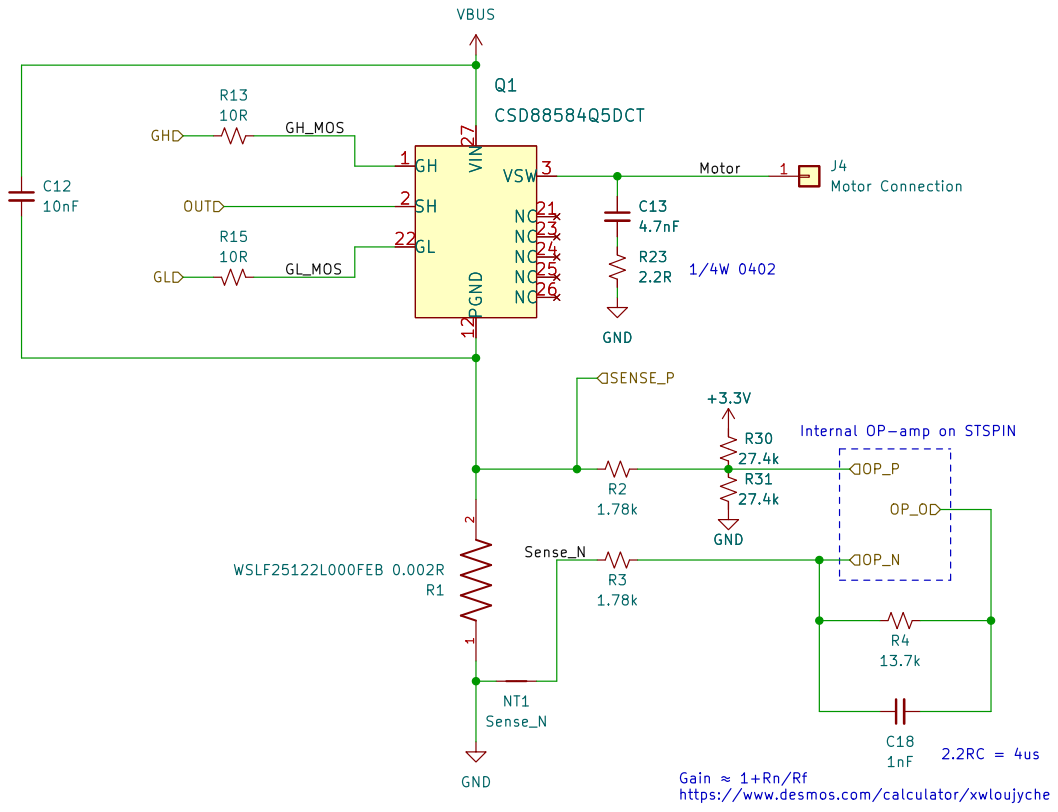
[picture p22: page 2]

Internal OP-amp on STSPIN

https://www.desmos.com/calculator/xwloujyche


Internal OP-amp on STSPIN

https://www.desmos.com/calculator/xwloujyche


Internal OP-amp on STSPIN

https://www.desmos.com/calculator/xwloujyche

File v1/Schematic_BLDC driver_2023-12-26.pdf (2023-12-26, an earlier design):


Drawn By: Christopher Xu









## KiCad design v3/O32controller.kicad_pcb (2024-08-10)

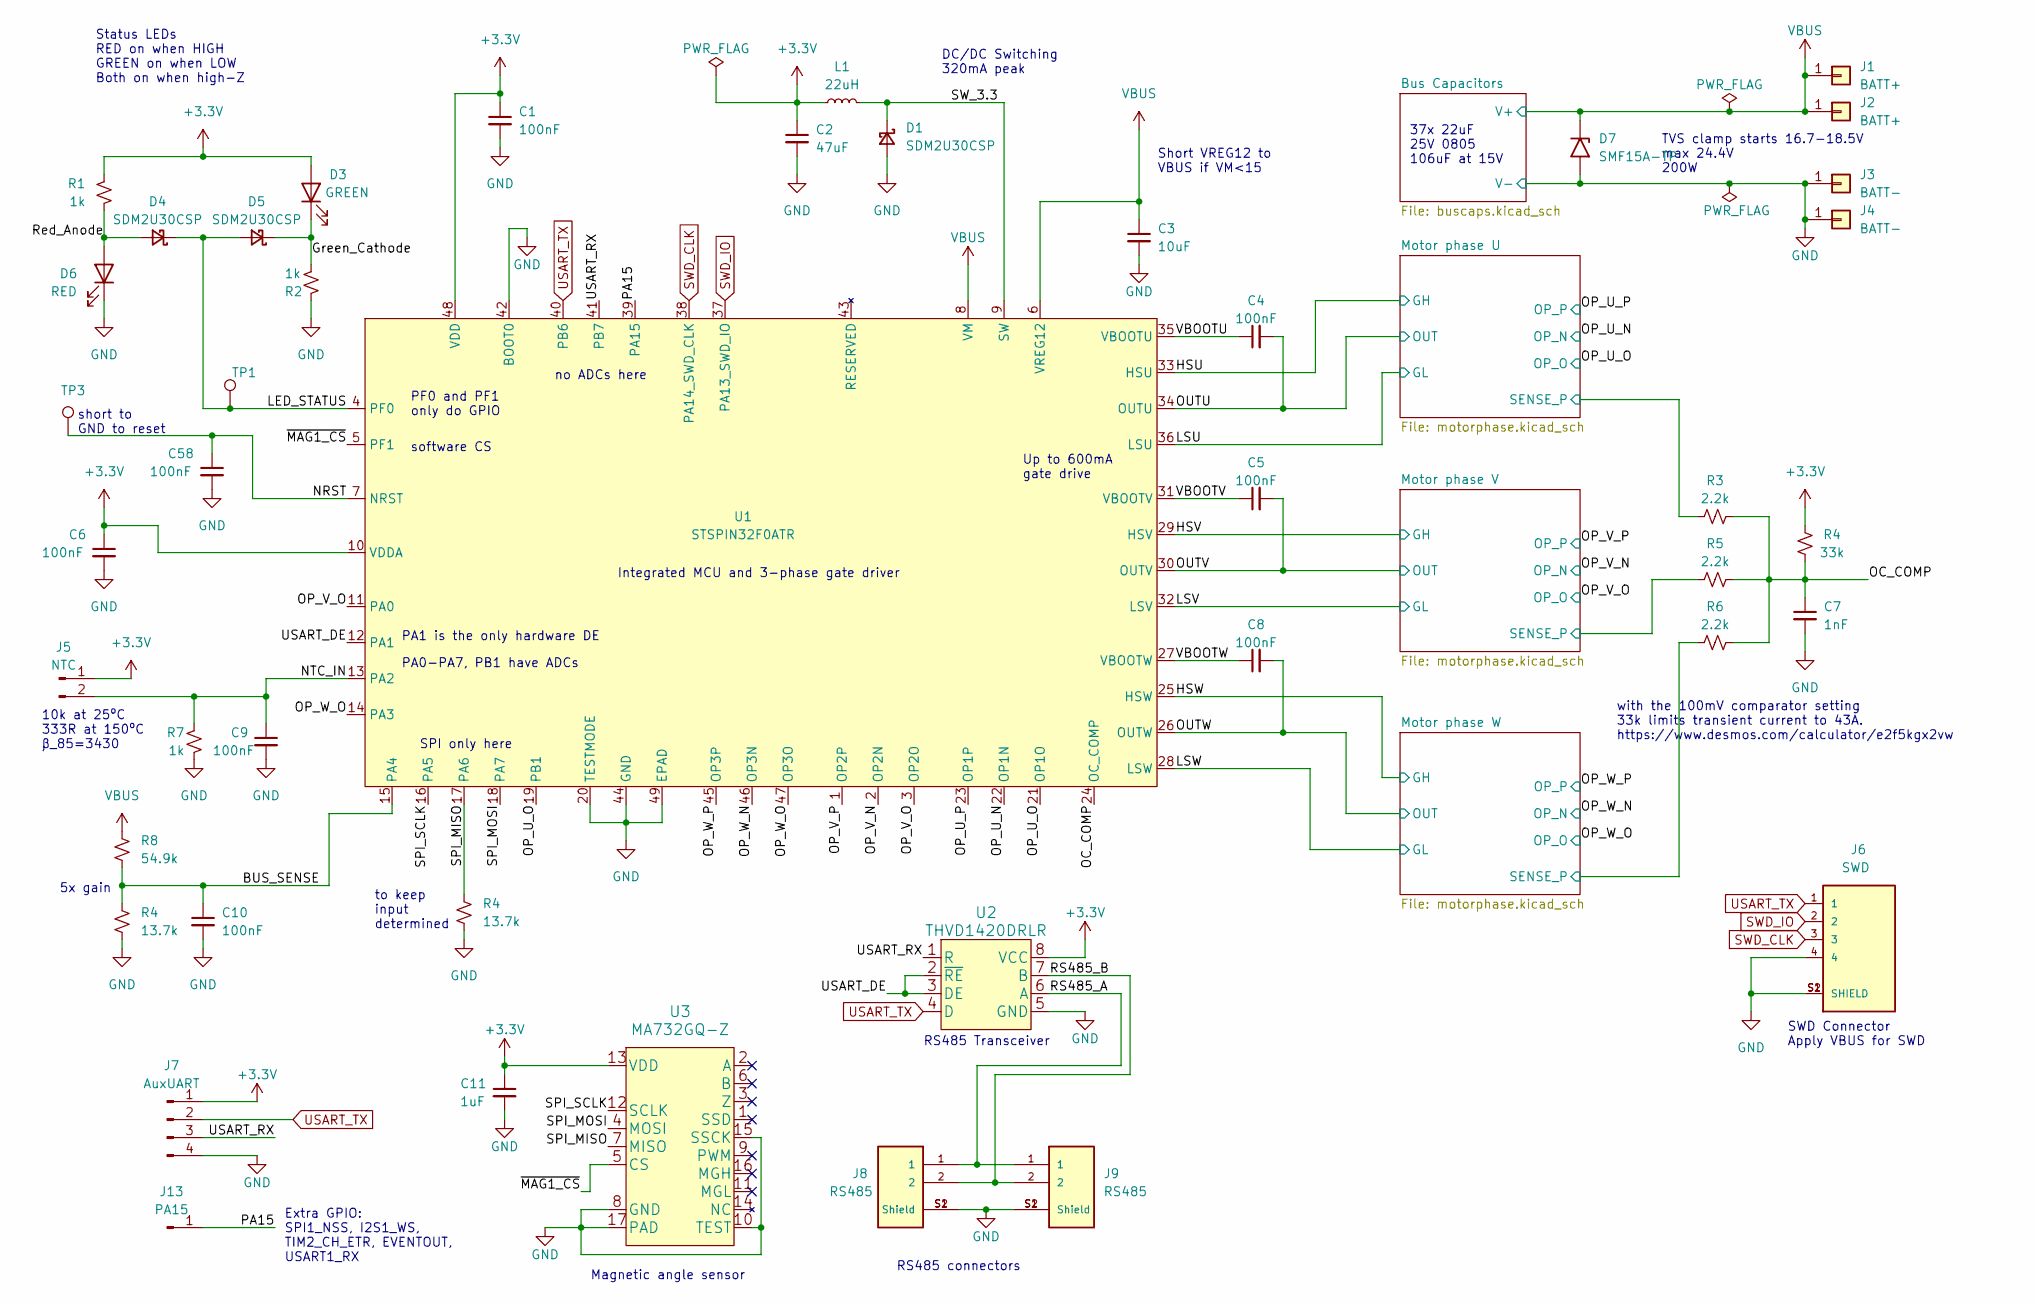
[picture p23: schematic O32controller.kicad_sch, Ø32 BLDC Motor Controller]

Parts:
C1, C4, C5, C6, C8, C9, C10, C58: 100nF; C_0402_1005Metric; MPN CL05B104KB54PNC; LCSC C307331
C2: 47uF; C_0603_1608Metric; MPN GRM188R60J476ME15D; LCSC C140782
C3: 10uF; C_0603_1608Metric; MPN GRM188R6YA106MA73D; LCSC C194427
C7: 1nF; C_0402_1005Metric; MPN 0402B102K500NT; LCSC C1523
C11: 1uF; C_0402_1005Metric; MPN CL05A105KA5NQNC; LCSC C52923
D1, D4, D5: SDM2U30CSP; SDM2U30CSP-7; MPN SDM2U30CSP-7
D3: GREEN; LED_0603_1608Metric; MPN LTST-C191KGKT; LCSC C125098
D6: RED; LED_0603_1608Metric; MPN KT-0603R; LCSC C2286
D7: SMF15A-TP; D_SMF; MPN SMF15A-TP; LCSC C914420
J1, J2: BATT+; SolderWire-Actual_1x01_D1.7mm_OD_2.75mm
J3, J4: BATT-; SolderWire-Actual_1x01_D1.7mm_OD_2.75mm
J5: NTC; SolderNTC-1.27mm
J6: SWD; JST_SM04B-SRSS-TB(LF)(SN); MPN SM04B-SRSS-TB(LF)(SN)
J7: AuxUART; SolderUART-1.27mm
J8, J9: RS485; JST_SM02B-SRSS-TB(LF)(SN); MPN SM02B-SRSS-TB_LF__SN_; LCSC C160402
J13: PA15; SolderPad1-1.27mm
L1: 22uH; IND_VLS201612CX-220M-1; MPN VLS201612CX-220M-1; LCSC C2044426
R1, R2, R7: 1k; R_0402_1005Metric; MPN 0402WGF1001TCE; LCSC C11702
R3, R5, R6: 2.2k; R_0402_1005Metric; MPN 0402WGF2201TCE; LCSC C25879
R4: 33k; R_0402_1005Metric; MPN 0402WGF3302TCE; LCSC C25779
R8: 54.9k; R_0402_1005Metric; MPN RC0402FR-0754K9L; LCSC C137959
TP1, TP3: TestPoint; TestPoint_Pad_Rect
U1: STSPIN32F0ATR; VFQFPN-48-1EP_7x7mm_P0.5mm_EP2.8x2.8mm; MPN STSPIN32F0ATR; LCSC C2651733
U2: THVD1420DRLR; THVD1420DRLR_SOT-585; MPN THVD1420DRLR
U3: MA732GQ-Z; QFN-16_MA732; MPN MA732GQ-Z

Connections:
/Green_Cathode: D3.1 (K), D5.1 (K), R2.1
/HSU: U1.33 (HSU); also elsewhere on the board
/HSV: U1.29 (HSV); also elsewhere on the board
/HSW: U1.25 (HSW); also elsewhere on the board
/LED_STATUS: D4.1 (K), D5.2 (A), TP1.1, U1.4 (PF0)
/LSU: U1.36 (LSU); also elsewhere on the board
/LSV: U1.32 (LSV); also elsewhere on the board
/LSW: U1.28 (LSW); also elsewhere on the board
/Motor phase U/SENSE_P: R3.2; also elsewhere on the board
/Motor phase V/SENSE_P: R5.2; also elsewhere on the board
/Motor phase W/SENSE_P: R6.2; also elsewhere on the board
/NRST: C58.1, TP3.1, U1.7 (NRST)
/NTC_IN: C9.1, J5.2, R7.2, U1.13 (PA2)
/OP_U_N: U1.22 (OP1N); also elsewhere on the board
/OP_U_O: U1.19 (PB1), U1.21 (OP1O); also elsewhere on the board
/OP_U_P: U1.23 (OP1P); also elsewhere on the board
/OP_V_N: U1.2 (OP2N); also elsewhere on the board
/OP_V_O: U1.3 (OP2O), U1.11 (PA0); also elsewhere on the board
/OP_V_P: U1.1 (OP2P); also elsewhere on the board
/OP_W_N: U1.46 (OP3N); also elsewhere on the board
/OP_W_O: U1.14 (PA3), U1.47 (OP3O); also elsewhere on the board
/OP_W_P: U1.45 (OP3P); also elsewhere on the board
/OUTU: C4.2, U1.34 (OUTU); also elsewhere on the board
/OUTV: C5.2, U1.30 (OUTV); also elsewhere on the board
/OUTW: C8.2, U1.26 (OUTW); also elsewhere on the board
/PA15: J13.1, U1.39 (PA15)
/RS485_A: J8.1, J9.1, U2.6 (A)
/RS485_B: J8.2, J9.2, U2.7 (B)
/Red_Anode: D4.2 (A), D6.2 (A), R1.1
/SPI_MOSI: U1.18 (PA7), U3.4 (MOSI)
/SPI_SCLK: U1.16 (PA5), U3.12 (SCLK)
/SW_3.3: D1.1 (K), L1.2, U1.9 (SW)
/USART_DE: U1.12 (PA1), U2.2 (~RE), U2.3 (DE)
/USART_RX: J7.3, U1.41 (PB7), U2.1 (R)
/VBOOTU: C4.1, U1.35 (VBOOTU)
/VBOOTV: C5.1, U1.31 (VBOOTV)
/VBOOTW: C8.1, U1.27 (VBOOTW)
/~MAG1_CS: U1.5 (PF1), U3.5 (CS)
SWD_CLK: J6.3, U1.38 (PA14_SWD_CLK)
SWD_IO: J6.2, U1.37 (PA13_SWD_IO)
USART_TX: J6.1, J7.2, U1.40 (PB6), U2.4 (D)
VBUS: C3.1, D7.1 (A1), J1.1, J2.1, R8.1, U1.6 (VREG12), U1.8 (VM); also elsewhere on the board

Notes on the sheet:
PA1 is the only hardware DE
to keep input determined
RS485 Transceiver
short to GND to reset
Short VREG12 to VBUS if VM<15
Up to 600mA gate drive
Extra GPIO: SPI1_NSS, I2S1_WS, TIM2_CH_ETR, EVENTOUT, USART1_RX
37x 22uF 25V 0805 106uF at 15V
DC/DC Switching 320mA peak
Integrated MCU and 3-phase gate driver
PF0 and PF1 only do GPIO
PA0-PA7, PB1 have ADCs
TVS clamp starts 16.7-18.5V max 24.4V 200W
10k at 25ºC 333R at 150ºC β_85=3430
with the 100mV comparator setting 33k limits transient current to 43A. https://www.desmos.com/calculator/e2f5kgx2vw
5x gain
no ADCs here
SPI only here
Magnetic angle sensor
RS485 connectors
software CS
SWD Connector Apply VBUS for SWD
Status LEDs RED on when HIGH GREEN on when LOW Both on when high-Z

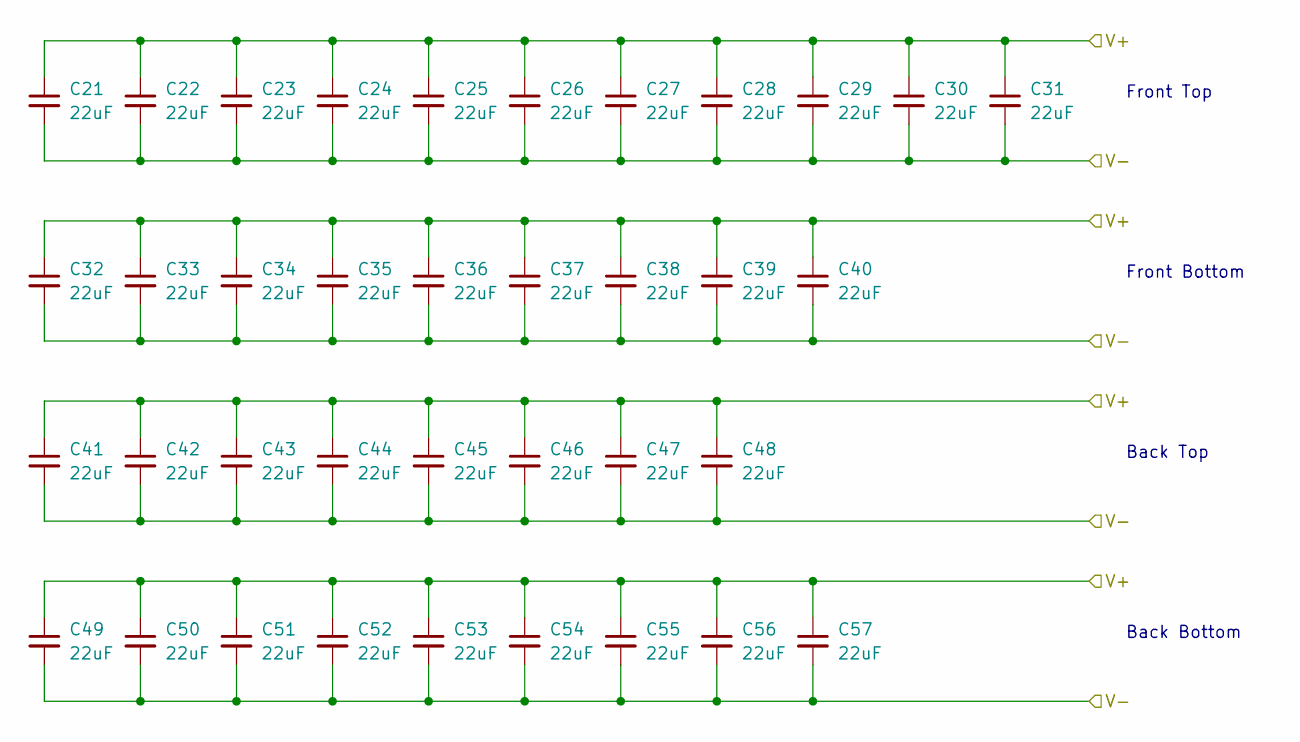
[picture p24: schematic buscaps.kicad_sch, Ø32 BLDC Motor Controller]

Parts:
C21, C22, C23, C24, C25, C26, C27, C28, C29, C30, C31, C32, C33, C34, C35, C36, C37, C38, C39, C40, C41, C42, C43, C44, C45, C46, C47, C48, C49, C50, C51, C52, C53, C54, C55, C56, C57: 22uF; C_0805_nosilk; MPN CL21A226MAQNNNE; LCSC C45783

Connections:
VBUS: C21.1, C22.1, C23.1, C24.1, C25.1, C26.1, C27.1, C28.1, C29.1, C30.1, C31.1, C32.1, C33.1, C34.1, C35.1, C36.1, C37.1, C38.1, C39.1, C40.1, C41.1, C42.1, C43.1, C44.1, C45.1, C46.1, C47.1, C48.1, C49.1, C50.1, C51.1, C52.1, C53.1, C54.1, C55.1, C56.1, C57.1; also elsewhere on the board

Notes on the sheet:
Back Bottom
Back Top
Front Top
Front Bottom

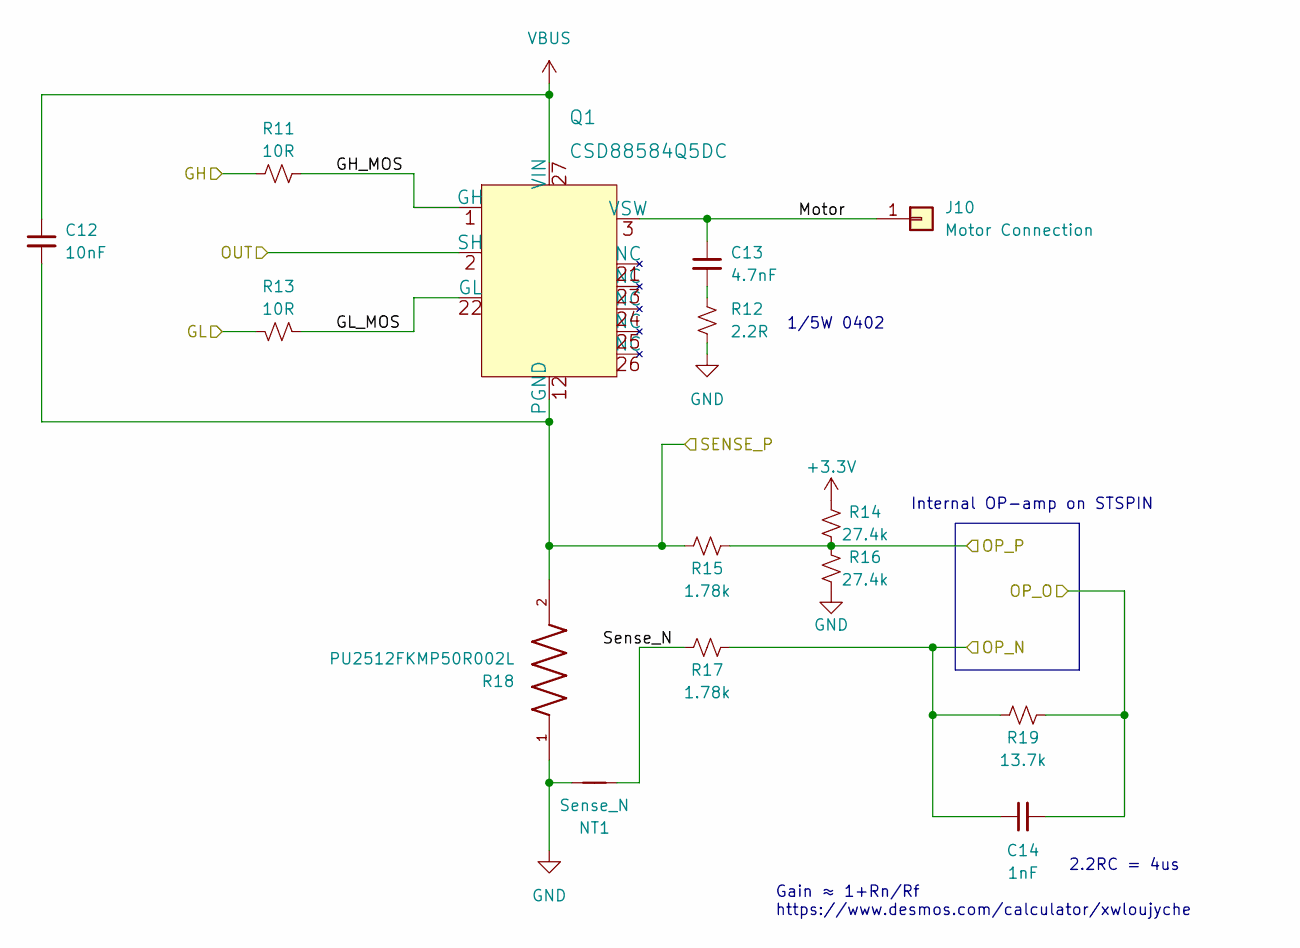
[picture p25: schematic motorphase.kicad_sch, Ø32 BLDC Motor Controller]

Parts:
C12: 10nF; C_0402_1005Metric; MPN CL05B103KB5NNNC; LCSC C15195
C13: 4.7nF; C_0402_1005Metric; MPN 0402B472K500NT; LCSC C1538
C14: 1nF; C_0402_1005Metric; MPN 0402B102K500NT; LCSC C1523
J10: Motor Connection; SolderWire-Actual_1x01_D1.7mm_OD_2.75mm
NT1: Sense_N; NetTie-2_SMD_Pad0.25mm
Q1: CSD88584Q5DC; CSD88584Q5DCT; MPN CSD88584Q5DC
R11, R13: 10R; R_0402_1005Metric; MPN SR0402FR-7T10RL; LCSC C854481
R12: 2.2R; R_0402_1005Metric; MPN RK73B1ETTP2R2J; LCSC C131536
R14, R16: 27.4k; R_0402_1005Metric; MPN RC0402FR-0727K4L; LCSC C273730
R15, R17: 1.78k; R_0402_1005Metric; MPN ARG02FTC1781; LCSC C284379
R18: PU2512FKMP50R002L; R_Shunt_2512_6332Metric; MPN PU2512FKMP50R002L; LCSC C2090861
R19: 13.7k; R_0402_1005Metric; MPN RC0402FR-0713K7L; LCSC C274888

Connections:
/HSU: R11.1; also elsewhere on the board
/LSU: R13.2; also elsewhere on the board
/Motor phase U/GH_MOS: Q1.1 (GH), R11.2
/Motor phase U/GL_MOS: Q1.22 (GL), R13.1
/Motor phase U/Motor: C13.1, J10.1, Q1.3 (VSW)
/Motor phase U/SENSE_P: C12.2, Q1.12 (PGND), R15.1, R18.2; also elsewhere on the board
/Motor phase U/Sense_N: NT1.1, R17.1
/OP_U_N: C14.1, R17.2, R19.1; also elsewhere on the board
/OP_U_O: C14.2, R19.2; also elsewhere on the board
/OP_U_P: R14.1, R15.2, R16.2; also elsewhere on the board
/OUTU: Q1.2 (SH); also elsewhere on the board
unnamed: C13.2, R12.1
VBUS: C12.1, Q1.27 (VIN); also elsewhere on the board

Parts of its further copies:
C15, C18: 10nF; C_0402_1005Metric; MPN CL05B103KB5NNNC; LCSC C15195
C16, C19: 4.7nF; C_0402_1005Metric; MPN 0402B472K500NT; LCSC C1538
C17, C20: 1nF; C_0402_1005Metric; MPN 0402B102K500NT; LCSC C1523
J11, J12: Motor Connection; SolderWire-Actual_1x01_D1.7mm_OD_2.75mm
NT2, NT3: Sense_N; NetTie-2_SMD_Pad0.25mm
Q2, Q3: CSD88584Q5DC; CSD88584Q5DCT; MPN CSD88584Q5DC
R20, R22, R29, R31: 10R; R_0402_1005Metric; MPN SR0402FR-7T10RL; LCSC C854481
R21, R30: 2.2R; R_0402_1005Metric; MPN RK73B1ETTP2R2J; LCSC C131536
R23, R25, R32, R34: 27.4k; R_0402_1005Metric; MPN RC0402FR-0727K4L; LCSC C273730
R24, R26, R33, R35: 1.78k; R_0402_1005Metric; MPN ARG02FTC1781; LCSC C284379
R27, R36: PU2512FKMP50R002L; R_Shunt_2512_6332Metric; MPN PU2512FKMP50R002L; LCSC C2090861
R28, R37: 13.7k; R_0402_1005Metric; MPN RC0402FR-0713K7L; LCSC C274888

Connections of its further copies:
/HSV: R20.1; also elsewhere on the board
/HSW: R29.1; also elsewhere on the board
/LSV: R22.2; also elsewhere on the board
/LSW: R31.2; also elsewhere on the board
/Motor phase V/GH_MOS: Q2.1 (GH), R20.2
/Motor phase V/GL_MOS: Q2.22 (GL), R22.1
/Motor phase V/Motor: C16.1, J11.1, Q2.3 (VSW)
/Motor phase V/SENSE_P: C15.2, Q2.12 (PGND), R24.1, R27.2; also elsewhere on the board
/Motor phase V/Sense_N: NT2.1, R26.1
/Motor phase W/GH_MOS: Q3.1 (GH), R29.2
/Motor phase W/GL_MOS: Q3.22 (GL), R31.1
/Motor phase W/Motor: C19.1, J12.1, Q3.3 (VSW)
/Motor phase W/SENSE_P: C18.2, Q3.12 (PGND), R33.1, R36.2; also elsewhere on the board
/Motor phase W/Sense_N: NT3.1, R35.1
/OP_V_N: C17.1, R26.2, R28.1; also elsewhere on the board
/OP_V_O: C17.2, R28.2; also elsewhere on the board
/OP_V_P: R23.1, R24.2, R25.2; also elsewhere on the board
/OP_W_N: C20.1, R35.2, R37.1; also elsewhere on the board
/OP_W_O: C20.2, R37.2; also elsewhere on the board
/OP_W_P: R32.1, R33.2, R34.2; also elsewhere on the board
/OUTV: Q2.2 (SH); also elsewhere on the board
/OUTW: Q3.2 (SH); also elsewhere on the board
unnamed: C16.2, R21.1
unnamed: C19.2, R30.1
VBUS: C15.1, C18.1, Q2.27 (VIN), Q3.27 (VIN); also elsewhere on the board

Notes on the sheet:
Internal OP-amp on STSPIN
2.2RC = 4us
Gain ≈ 1+Rn/Rf https://www.desmos.com/calculator/xwloujyche
1/5W 0402

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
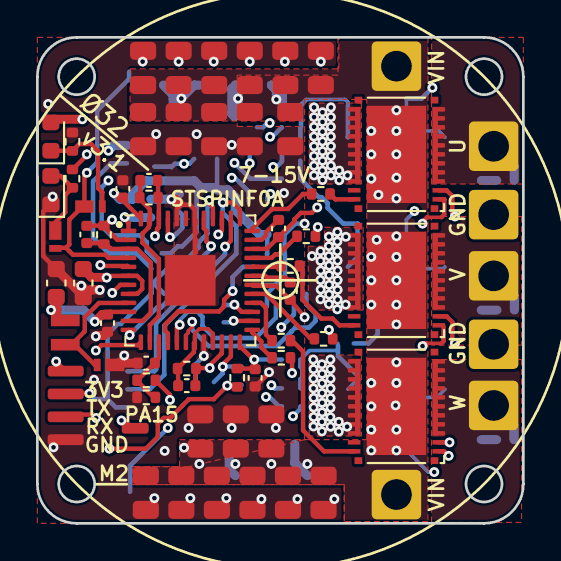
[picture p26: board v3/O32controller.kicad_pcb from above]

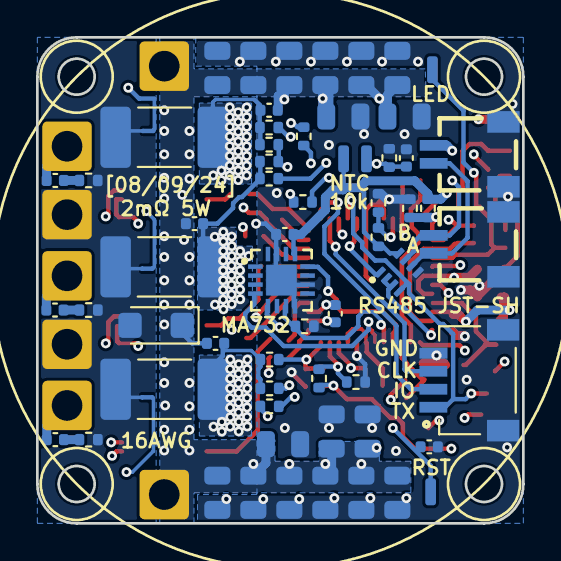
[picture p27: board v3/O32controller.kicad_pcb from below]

Board: 4 copper layers, 27.0 x 27.0 mm, 126 parts (62 on the bottom side), 62 nets.

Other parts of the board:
R9, R10: 13.7k; R_0402_1005Metric

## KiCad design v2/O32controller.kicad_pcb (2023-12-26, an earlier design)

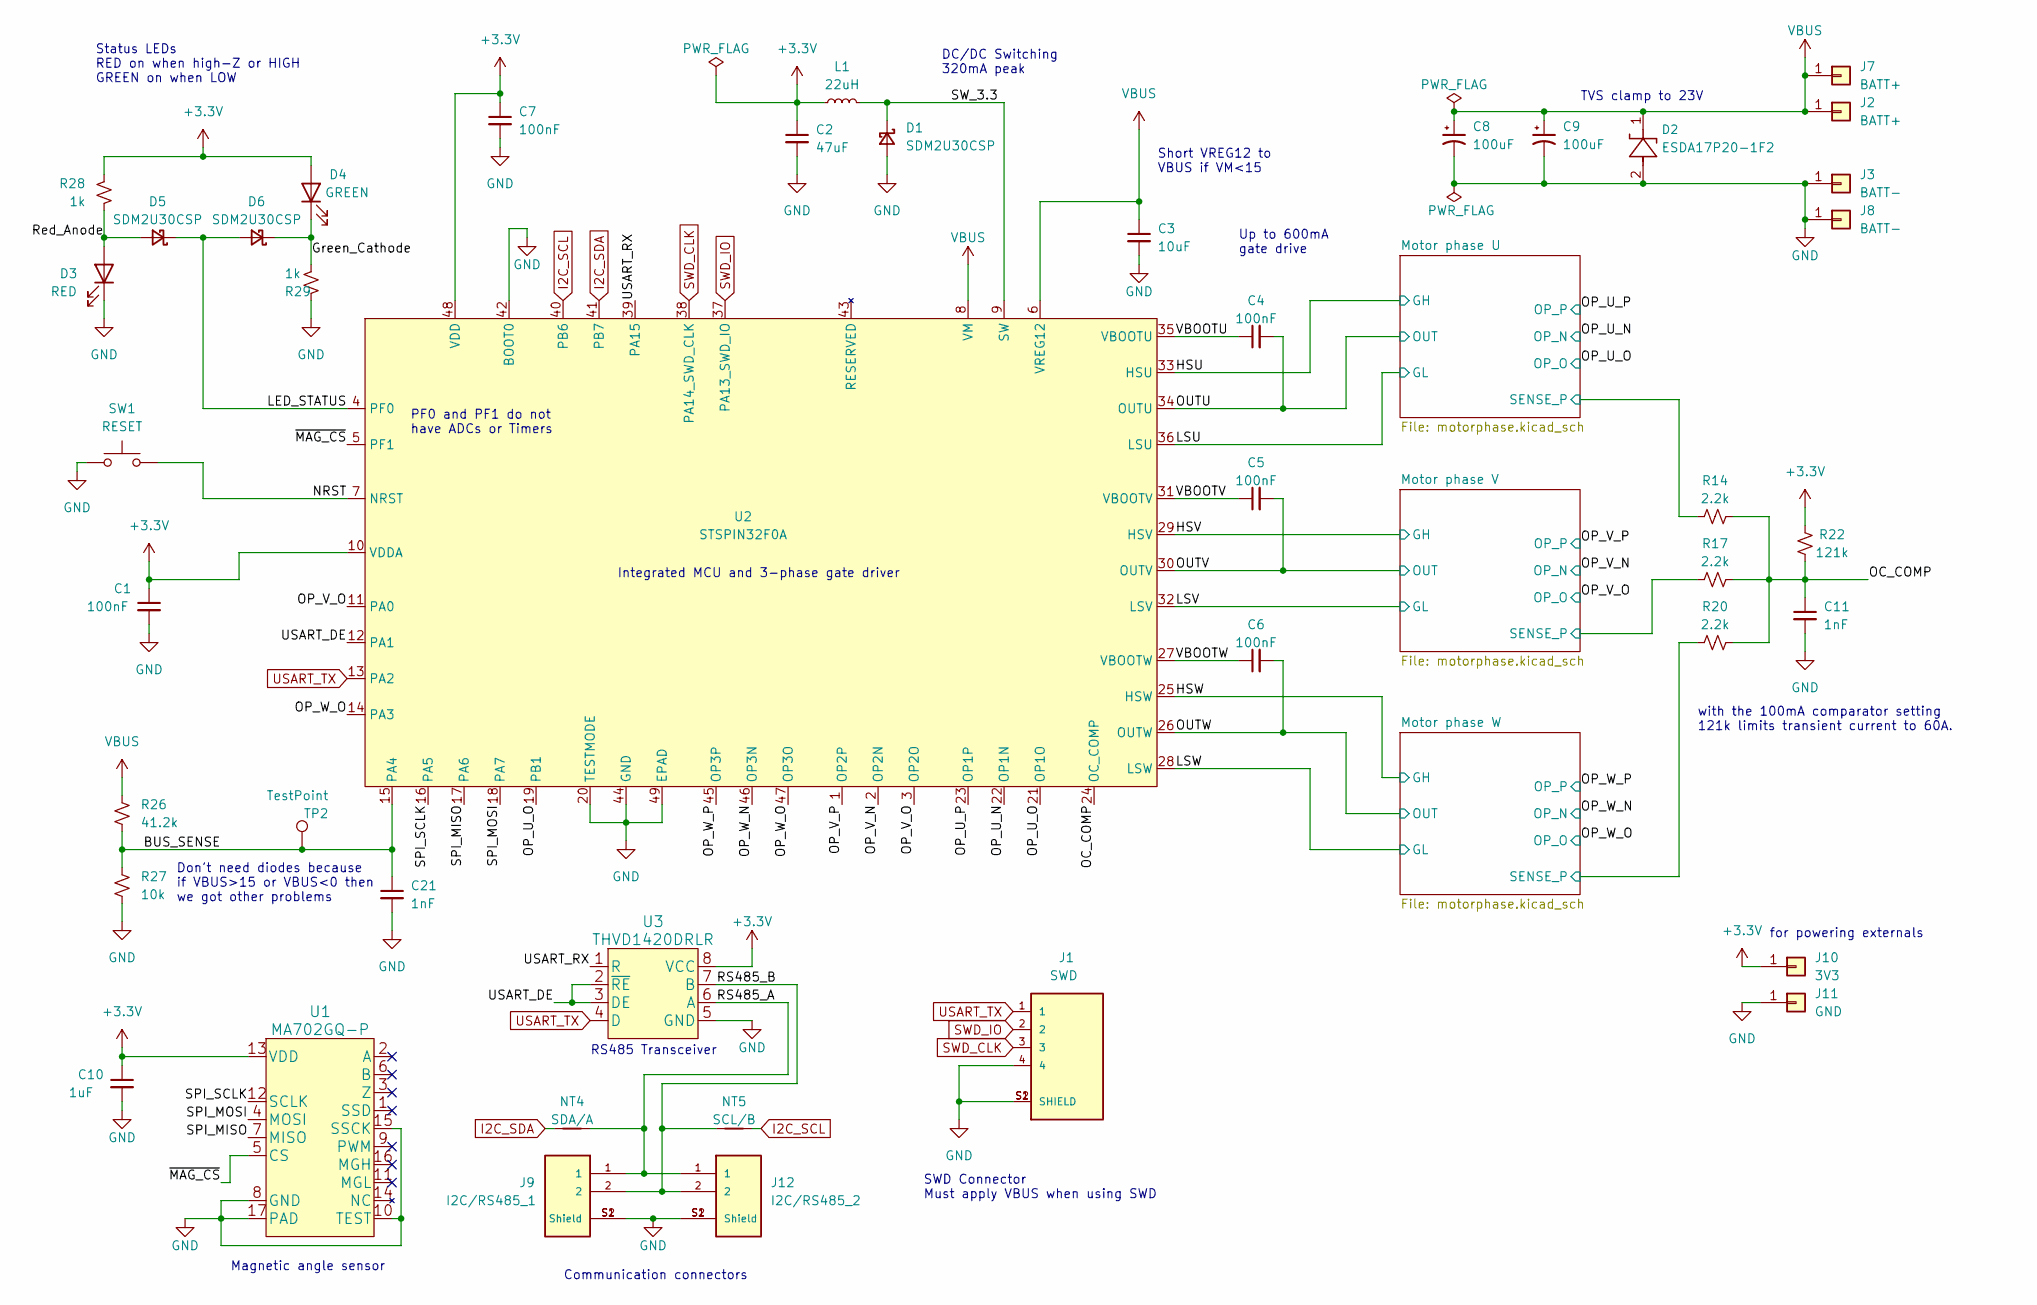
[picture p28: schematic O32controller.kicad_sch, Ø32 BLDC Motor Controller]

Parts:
C1, C4, C5, C6, C7: 100nF; C_0402_1005Metric
C2: 47uF; C_0603_1608Metric
C3: 10uF; C_0603_1608Metric
C8, C9: 100uF; CAP_EEEFN1E101UP
C10: 1uF; C_0402_1005Metric
C11, C21: 1nF; C_0402_1005Metric
D1, D5, D6: SDM2U30CSP; SDM2U30CSP-7
D2: ESDA17P20-1F2; SMT2_0P91X0P63_STM-L
D3: RED; LED_0603_1608Metric
D4: GREEN; LED_0603_1608Metric
J1: SWD; JST_SM04B-SRSS-TB(LF)(SN)
J2, J7: BATT+; SolderWire-Actual_1x01_D1.7mm_OD_2.75mm
J3, J8: BATT-; SolderWire-Actual_1x01_D1.7mm_OD_2.75mm
J9: I2C/RS485_1; JST_SM02B-SRSS-TB(LF)(SN)
J10: 3V3; SolderWire-Actual_1x01_D1.25mm_OD_1.8mm
J11: GND; SolderWire-Actual_1x01_D1.25mm_OD_1.8mm
J12: I2C/RS485_2; JST_SM02B-SRSS-TB(LF)(SN)
L1: 22uH; IND_VLS201612CX-220M-1
NT4: SDA/A; NetTie-2_SMD_Pad0.25mm
NT5: SCL/B; NetTie-2_SMD_Pad0.25mm
R14, R17, R20: 2.2k; R_0402_1005Metric
R22: 121k; R_0402_1005Metric
R26: 41.2k; R_0402_1005Metric
R27: 10k; R_0402_1005Metric
R28, R29: 1k; R_0402_1005Metric
SW1: RESET; Tactile_Switch_EVQ-P7A01P
TP2: TestPoint; TestPoint_Pad_D1.0mm
U1: MA702GQ-P
U2: STSPIN32F0A; VFQFPN-48-1EP_7x7mm_P0.5mm_EP2.8x2.8mm
U3: THVD1420DRLR; THVD1420DRLR_SOT-585

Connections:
+3.3V: C1.1, C2.1, C7.1, C10.1, D4.2 (A), J10.1, L1.1, R22.1, R28.2, U1.13 (VDD), U2.10 (VDDA), U2.48 (VDD), U3.8 (VCC); also elsewhere on the board
/BUS_SENSE: C21.1, R26.2, R27.1, TP2.1, U2.15 (PA4)
/Green_Cathode: D4.1 (K), D6.1 (K), R29.1
/HSU: U2.33 (HSU); also elsewhere on the board
/HSV: U2.29 (HSV); also elsewhere on the board
/HSW: U2.25 (HSW); also elsewhere on the board
/LED_STATUS: D5.1 (K), D6.2 (A), U2.4 (PF0)
/LSU: U2.36 (LSU); also elsewhere on the board
/LSV: U2.32 (LSV); also elsewhere on the board
/LSW: U2.28 (LSW); also elsewhere on the board
/Motor phase U/SENSE_P: R14.2; also elsewhere on the board
/Motor phase V/SENSE_P: R17.2; also elsewhere on the board
/Motor phase W/SENSE_P: R20.2; also elsewhere on the board
/NRST: SW1.2, U2.7 (NRST)
/OC_COMP: C11.1, R14.1, R17.1, R20.1, R22.2, U2.24 (OC_COMP)
/OP_U_N: U2.22 (OP1N); also elsewhere on the board
/OP_U_O: U2.19 (PB1), U2.21 (OP1O); also elsewhere on the board
/OP_U_P: U2.23 (OP1P); also elsewhere on the board
/OP_V_N: U2.2 (OP2N); also elsewhere on the board
/OP_V_O: U2.3 (OP2O), U2.11 (PA0); also elsewhere on the board
/OP_V_P: U2.1 (OP2P); also elsewhere on the board
/OP_W_N: U2.46 (OP3N); also elsewhere on the board
/OP_W_O: U2.14 (PA3), U2.47 (OP3O); also elsewhere on the board
/OP_W_P: U2.45 (OP3P); also elsewhere on the board
/OUTU: C4.2, U2.34 (OUTU); also elsewhere on the board
/OUTV: C5.2, U2.30 (OUTV); also elsewhere on the board
/OUTW: C6.2, U2.26 (OUTW); also elsewhere on the board
/RS485_A: J9.1, J12.1, NT4.2, U3.6 (A)
/RS485_B: J9.2, J12.2, NT5.2, U3.7 (B)
/Red_Anode: D3.2 (A), D5.2 (A), R28.1
/SPI_MISO: U1.7 (MISO), U2.17 (PA6)
/SPI_MOSI: U1.4 (MOSI), U2.18 (PA7)
/SPI_SCLK: U1.12 (SCLK), U2.16 (PA5)
/SW_3.3: D1.1 (K), L1.2, U2.9 (SW)
/USART_DE: U2.12 (PA1), U3.2 (~RE), U3.3 (DE)
/USART_RX: U2.39 (PA15), U3.1 (R)
/VBOOTU: C4.1, U2.35 (VBOOTU)
/VBOOTV: C5.1, U2.31 (VBOOTV)
/VBOOTW: C6.1, U2.27 (VBOOTW)
/~MAG_CS: U1.5 (CS), U2.5 (PF1)
GND: C1.2, C2.2, C3.2, C7.2, C8.2, C9.2, C10.2, C11.2, C21.2, D1.2 (A), D2.2, D3.1 (K), J1.4, J1.S1 (SHIELD), J1.S2 (SHIELD), J3.1, J8.1, J9.S1 (Shield), J9.S2 (Shield), J11.1, J12.S1 (Shield), J12.S2 (Shield), R27.2, R29.2, SW1.1, U1.8 (GND), U1.10 (TEST), U1.15 (SSCK), U1.17 (PAD), U2.20 (TESTMODE), U2.42 (BOOT0), U2.44 (GND), U2.49 (EPAD), U3.5 (GND); also elsewhere on the board
I2C_SCL: NT5.1, U2.40 (PB6)
I2C_SDA: NT4.1, U2.41 (PB7)
SWD_CLK: J1.3, U2.38 (PA14_SWD_CLK)
SWD_IO: J1.2, U2.37 (PA13_SWD_IO)
USART_TX: J1.1, U2.13 (PA2), U3.4 (D)
VBUS: C3.1, C8.1, C9.1, D2.1, J2.1, J7.1, R26.1, U2.6 (VREG12), U2.8 (VM); also elsewhere on the board

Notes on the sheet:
RS485 Transceiver
PF0 and PF1 do not have ADCs or Timers
Short VREG12 to VBUS if VM<15
Up to 600mA gate drive
DC/DC Switching 320mA peak
Integrated MCU and 3-phase gate driver
TVS clamp to 23V
with the 100mA comparator setting 121k limits transient current to 60A.
Don't need diodes because if VBUS>15 or VBUS<0 then we got other problems
Magnetic angle sensor
Communication connectors
SWD Connector Must apply VBUS when using SWD
for powering externals
Status LEDs RED on when high-Z or HIGH GREEN on when LOW

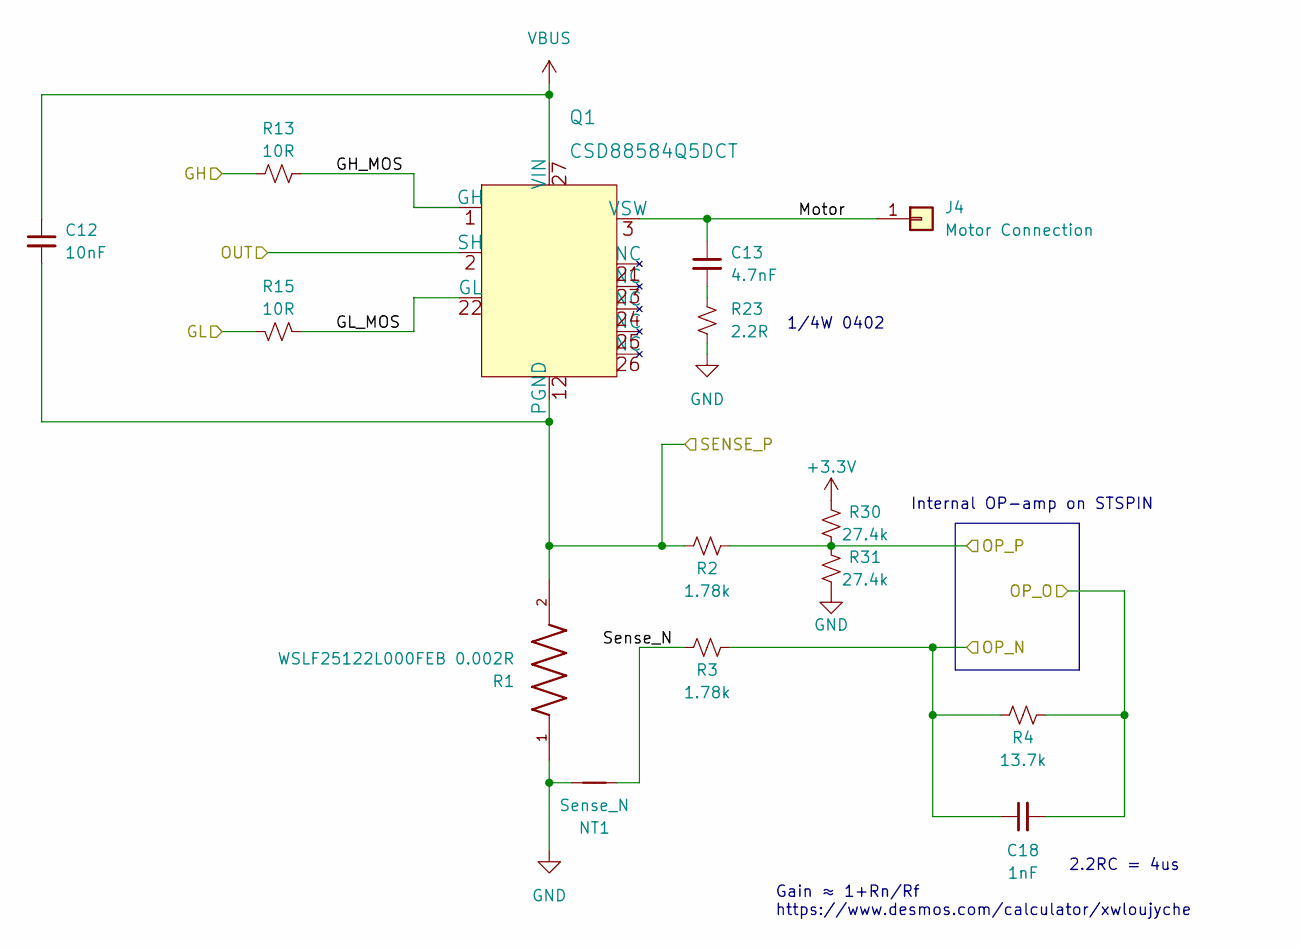
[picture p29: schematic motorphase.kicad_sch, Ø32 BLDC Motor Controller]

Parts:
C12: 10nF; C_0402_1005Metric
C13: 4.7nF; C_0402_1005Metric
C18: 1nF; C_0402_1005Metric
J4: Motor Connection; SolderWire-Actual_1x01_D1.7mm_OD_2.75mm
NT1: Sense_N; NetTie-2_SMD_Pad0.25mm
Q1: CSD88584Q5DCT
R1: WSLF25122L000FEB 0.002R; R_Shunt_2512_6332Metric
R2, R3: 1.78k; R_0402_1005Metric
R4: 13.7k; R_0402_1005Metric
R13, R15: 10R; R_0402_1005Metric
R23: 2.2R; R_0402_1005Metric
R30, R31: 27.4k; R_0402_1005Metric

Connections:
+3.3V: R30.2; also elsewhere on the board
/HSU: R13.1; also elsewhere on the board
/LSU: R15.2; also elsewhere on the board
/Motor phase U/GH_MOS: Q1.1 (GH), R13.2
/Motor phase U/GL_MOS: Q1.22 (GL), R15.1
/Motor phase U/Motor: C13.1, J4.1, Q1.3 (VSW)
/Motor phase U/SENSE_P: C12.2, Q1.12 (PGND), R1.2, R2.1; also elsewhere on the board
/Motor phase U/Sense_N: NT1.1, R3.1
/OP_U_N: C18.1, R3.2, R4.1; also elsewhere on the board
/OP_U_O: C18.2, R4.2; also elsewhere on the board
/OP_U_P: R2.2, R30.1, R31.2; also elsewhere on the board
/OUTU: Q1.2 (SH); also elsewhere on the board
GND: NT1.2, R1.1, R23.2, R31.1; also elsewhere on the board
unnamed: C13.2, R23.1
VBUS: C12.1, Q1.27 (VIN); also elsewhere on the board

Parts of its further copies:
C14, C16: 10nF; C_0402_1005Metric
C15, C17: 4.7nF; C_0402_1005Metric
C19, C20: 1nF; C_0402_1005Metric
J5, J6: Motor Connection; SolderWire-Actual_1x01_D1.7mm_OD_2.75mm
NT2, NT3: Sense_N; NetTie-2_SMD_Pad0.25mm
Q2, Q3: CSD88584Q5DCT
R5, R9: WSLF25122L000FEB 0.002R; R_Shunt_2512_6332Metric
R6, R7, R10, R11: 1.78k; R_0402_1005Metric
R8, R12: 13.7k; R_0402_1005Metric
R16, R18, R19, R21: 10R; R_0402_1005Metric
R24, R25: 2.2R; R_0402_1005Metric
R32, R33, R34, R35: 27.4k; R_0402_1005Metric

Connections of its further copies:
+3.3V: R32.2, R34.2; also elsewhere on the board
/HSV: R16.1; also elsewhere on the board
/HSW: R19.1; also elsewhere on the board
/LSV: R18.2; also elsewhere on the board
/LSW: R21.2; also elsewhere on the board
/Motor phase V/GH_MOS: Q2.1 (GH), R16.2
/Motor phase V/GL_MOS: Q2.22 (GL), R18.1
/Motor phase V/Motor: C15.1, J5.1, Q2.3 (VSW)
/Motor phase V/SENSE_P: C14.2, Q2.12 (PGND), R5.2, R6.1; also elsewhere on the board
/Motor phase V/Sense_N: NT2.1, R7.1
/Motor phase W/GH_MOS: Q3.1 (GH), R19.2
/Motor phase W/GL_MOS: Q3.22 (GL), R21.1
/Motor phase W/Motor: C17.1, J6.1, Q3.3 (VSW)
/Motor phase W/SENSE_P: C16.2, Q3.12 (PGND), R9.2, R10.1; also elsewhere on the board
/Motor phase W/Sense_N: NT3.1, R11.1
/OP_V_N: C19.1, R7.2, R8.1; also elsewhere on the board
/OP_V_O: C19.2, R8.2; also elsewhere on the board
/OP_V_P: R6.2, R32.1, R33.2; also elsewhere on the board
/OP_W_N: C20.1, R11.2, R12.1; also elsewhere on the board
/OP_W_O: C20.2, R12.2; also elsewhere on the board
/OP_W_P: R10.2, R34.1, R35.2; also elsewhere on the board
/OUTV: Q2.2 (SH); also elsewhere on the board
/OUTW: Q3.2 (SH); also elsewhere on the board
GND: NT2.2, NT3.2, R5.1, R9.1, R24.2, R25.2, R33.1, R35.1; also elsewhere on the board
unnamed: C15.2, R24.1
unnamed: C17.2, R25.1
VBUS: C14.1, C16.1, Q2.27 (VIN), Q3.27 (VIN); also elsewhere on the board

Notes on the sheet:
Internal OP-amp on STSPIN
2.2RC = 4us
Gain ≈ 1+Rn/Rf https://www.desmos.com/calculator/xwloujyche
1/4W 0402

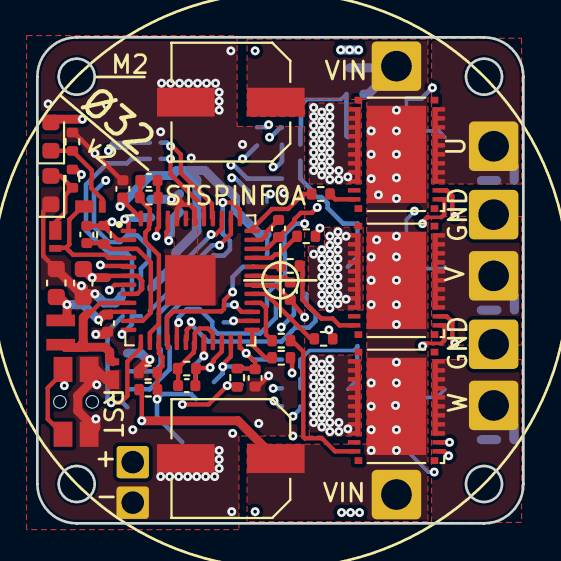
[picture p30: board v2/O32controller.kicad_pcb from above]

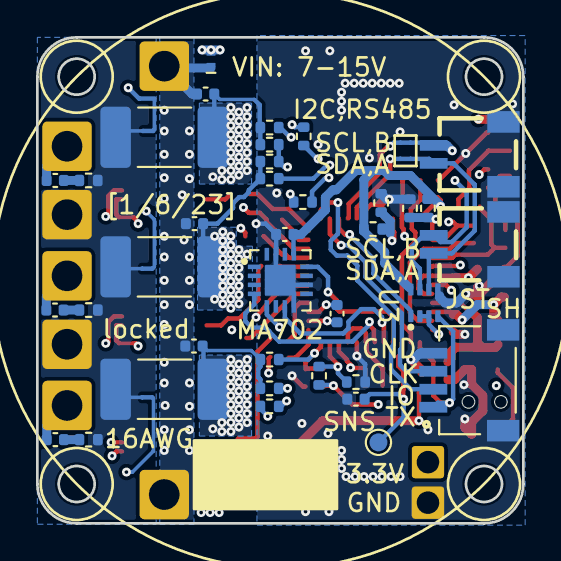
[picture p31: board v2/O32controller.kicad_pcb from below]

Board: 4 copper layers, 27.0 x 27.0 mm, 88 parts (42 on the bottom side), 62 nets.

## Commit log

2022-12-17 the beginning :)
    [O32controller.kicad_pcb, O32controller.kicad_sch, motorphase.kicad_sch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]
2022-12-21 more placement
    [O32controller.kicad_pcb, O32controller.kicad_sch, motorphase.kicad_sch]
2022-12-21 put everything on, need to choose caps
    [O32controller.kicad_pcb, O32controller.kicad_sch, motorphase.kicad_sch]
2022-12-21 fixed DRC, added as5047D, caps, ind
    [O32controller.kicad_pcb]
2022-12-25 before big shunt:
    [O32controller.kicad_pcb, O32controller.kicad_sch, motorphase.kicad_sch]
2022-12-25 used 2512 shunts to bridge vias
    [O32controller.kicad_pcb, O32controller.kicad_sch, motorphase.kicad_sch]
2022-12-25 ran into problem routing ground trace
    [O32controller.kicad_pcb]
2022-12-25 nope I don't think separated motor conns work
    [O32controller.kicad_pcb]
2022-12-25 routed some more
    [O32controller.kicad_pcb, O32controller.kicad_sch, motorphase.kicad_sch]
2022-12-25 routed some sense, netties, fixed NC
    [O32controller.kicad_pcb, O32controller.kicad_sch, motorphase.kicad_sch]
2022-12-26 routed most of power stage, no drc violations
    [O32controller.kicad_pcb, O32controller.kicad_sch]
2022-12-26 trying to fix shunt footprint:
    [O32controller.kicad_pcb, O32controller.kicad_sch, motorphase.kicad_sch]
2022-12-26 fixed clearances
    [O32controller.kicad_pcb]
2022-12-26 routed more signals
    [O32controller.kicad_pcb, O32controller.kicad_sch, motorphase.kicad_sch]
2022-12-27 just need to figure out gpio and buck
    [O32controller.kicad_pcb, O32controller.kicad_sch]
2022-12-28 i don't like CAN
    [O32controller.kicad_pcb, motorphase.kicad_sch]
2022-12-28 assigned gpio and adcs
    [O32controller.kicad_pcb, O32controller.kicad_sch]
2023-01-01 added mag702, leds, thought about tx out:
    [O32controller.kicad_pcb, O32controller.kicad_sch, motorphase.kicad_sch]
2023-01-03 added rs485 and placed ma702
    [O32controller.kicad_pcb, O32controller.kicad_sch, motorphase.kicad_sch]
2023-01-04 ahh my resistor schematic is old:
    [O32controller.kicad_sch, motorphase.kicad_sch]
2023-01-05 woohoo everything connected, no drc err
    [O32controller.kicad_pcb, O32controller.kicad_sch, motorphase.kicad_sch]
2023-01-05 choose led, tvs, start on silkscreen
    [O32controller.kicad_pcb, motorphase.kicad_sch]
2023-01-06 silkscreen pretty much done
    [O32controller.kicad_pcb, O32controller.kicad_sch]
2023-01-06 finish, generate gerbers
    [O32controller-B_Cu.gbl, O32controller-B_Mask.gbs, O32controller-B_Paste.gbp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]
2023-01-06 fix mosfet soldermask
    [O32controller-B_Cu.gbl, O32controller-B_Mask.gbs, O32controller-B_Paste.gbp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]
2023-08-23 add front and back pcb view pics
2023-12-26 clean up v2, fix libraries, netties, fix TVS dir
    [O32controller.kicad_pcb, O32controller.kicad_sch, motorphase.kicad_sch]
2023-12-26 remove motor conn from ibom, reannotate tvs diode
    [O32controller.kicad_pcb, O32controller.kicad_sch, motorphase.kicad_sch]
2023-12-26 restructure into v1,v2,v3 folders
    [O32controller-B_Cu.gbl, O32controller-B_Mask.gbs, O32controller-B_Paste.gbp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]
2023-12-27 external spi, update bus sns res, routing
    [O32controller.kicad_pcb, O32controller.kicad_sch, buscaps.kicad_sch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]
2023-12-27 bus caps, finished routing?
    [O32controller.kicad_pcb, O32controller.kicad_sch, buscaps.kicad_sch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]
2023-12-28 add stitching vias, 0 drc errors
    [O32controller.kicad_pcb]
2023-12-28 import pcbway cheapest capability drc rules
    [O32controller.kicad_pcb, O32controller.kicad_sch]
2023-12-28 increase vias to 0.25 hole 0.55 dia
    [O32controller.kicad_pcb]
2023-12-29 export for PCBway
    [BOM_O32controller.kicad_pcb.xls, Centroid_O32controller.kicad_pcb.xls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]
2023-12-30 o12encoder has spi and rs485 option w mcu
    [O32controller.kicad_pcb]
2023-12-30 forgot to add o12 directory
    [O12encoder.kicad_pcb, O12encoder.kicad_sch, encoder_outline.dxf]
2023-12-30 encoder change to both sides FFC
    [O12encoder.kicad_pcb, O12encoder.kicad_sch]
2023-12-30 undo autoroute
    [O12encoder.kicad_pcb, O12encoder.kicad_sch]
2023-12-30 Revert "encoder change to both sides FFC"
    This reverts commit 631d04212b57ce457fbe4c2d518c1d39f3519578.
    [O12encoder.kicad_pcb, O12encoder.kicad_sch]
2023-12-30 use kicad backup 2am
    [O12encoder.kicad_pcb]
2023-12-30 routed more, trouble with 3.3 and gnd
    [O12encoder.kicad_pcb, O12encoder.kicad_sch]
2023-12-31 done? added silkscreen and pa0 breakout
    [O12encoder.kicad_pcb, O12encoder.kicad_sch]
2023-12-31 clean up schematic
    [O12encoder.kicad_sch]
2024-01-03 heatsink step, generate Ø12encoder gerbers:
    [O12encoder-B_Cu.gbl, O12encoder-B_Mask.gbs, O12encoder-B_Paste.gbp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]
2024-01-28 update readme pic
    [O12encoder.kicad_sch]
2024-03-25 fixed note with OC comparator, 60A 121k error
    [O12encoder-B_Cu.gbl, O12encoder-B_Mask.gbs, O12encoder-B_Paste.gbp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]
2024-07-29 use MA732 instead of 702, SMF15A
    [O32controller.kicad_pcb, O32controller.kicad_sch, bom_jlc.csv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]
2024-07-30 finalize BOM for v3.1, shared w Axlab
    [O32controller.csv, O32controller.kicad_pcb, O32controller.kicad_sch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]
2024-08-10 v3.1 design done, replaced aux spi with uart and 1 gpio, bigger TVS, and MA732
    [O32controller.kicad_pcb, O32controller.kicad_sch, buscaps.kicad_sch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]
2024-08-10 release v3.1 and generate gerbers
    [BOM_O32controller.kicad_pcb.xls, Centroid_O32controller.kicad_pcb.xls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]
2024-08-10 rename order version and add schematic to readme
    [bom_jlcpcb.csv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]
